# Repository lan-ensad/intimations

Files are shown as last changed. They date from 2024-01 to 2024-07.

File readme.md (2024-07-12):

# Intimations of Shanshui

<!-- TOC -->
- [Interactive Sculpture](#interactive-sculpture)
  - [Interaction & Space Mapping Logic](#interaction--space-mapping-logic)
  - [network diagram](#network-diagram)
  - [mechanics](#mechanics)
  - [electronics](#electronics)
- [Installation](#installation)
  - [Raspberry](#raspberry)
    - [DAC+](#dac)
    - [NodeRed](#nodered)
    - [Pure Data](#pure-data)
    - [Mosquitto](#mosquitto)
<!-- /TOC -->

## Interactive Sculpture



|||
|--|--|
|Artists/Creators|Vivian Wang, Martin De Bie, Olivier Bienz|
|Title, Year|Intimations of Shanshui, 2024|
|Exhibition Location|Shanshui: Echoes & Signals, M+ Hong Kong|
|Media|Interactive textile sculpture with sound, light, movement, and sensors|
|Logic/Description|For Intimations, we created a structural concept around the idea of circular layers. This sculpture crafted from fabric creates a focused and immersive experience blending sound, movement, and light. Variations in sound, light and movement respond to human presence and circumnavigation, unfolding in a slow and deliberate choreography of the different elements. The work is an ode to Shanshui painting, bridging tradition and modernity through an interactive exchange and the composition of textile and sound, with special detail given to how lighting dramatically alters the visual impact of the mountains.|
|||

### Interaction & Space Mapping Logic

There are 6 distance sensors on the sculpture. They are labelled S_00 to S_05. S_02 and S_05 are at the entry and exit points of the display location called the Breakout Room. To trigger sound and light activity, we partitioned the interaction zones into 6 zones labelled A, B, C, D, E and F.

**Sounds** are activated by presence within zones. All zones have an inner and an outer zone and these measurements are not the same for each zone. The rationale is to have something a little more organic in shape. For example, Zone D has an inner zone that goes up to 500mm, and its outer zone extends up to 2000mm whereas Zone F has an inner zone of 400mm and the outer extends only up to 1100mm. Anything outside of 1100mm will register a value on the sensor but it will not trigger a sound. We also programmed sounds to trigger when 2 zones register a value at the same time, meaning the sensors in these zones have to sense two separate persons in order to activate a sound. Certain sounds will also only trigger after a delay value of say 29656ms in the outer zone of Zone D. This gives some nuance and variation to the sounds and does not create cacophony for every interaction that happens each time a sensor value is registered. These 2-zone combinations are also varied between inner and outer zones. For each specific zone within zones A-F, there are also sometimes 2 or 3 files that are randomised to create more diverse combinations of sounds.

**Light** colour combinations are also varied. Each concentric circle has between 3-5 sectors of LEDs that light up. The colour sectors are irregular, so as to create organic combinations of light and shadow play between the layers of textile. Different behaviours are triggered depending of how many zones are active during a certain amount of time. Each colour sequence is scripted to create a sense of rhythm and movement and the colours are selected according to a predefined colour palette.

**Movement** of the 4 circular rings/layers of textile mountains are programmed and follow its own logic. Between 90000ms to 120000ms, different combinations of rings 1,2,3 will move. The duration of movement varies between 3000ms and 20000ms. The direction of the oscillation is randomised. The rings could move in the same direction or in opposite directions. Once a day, all 4 rings move.

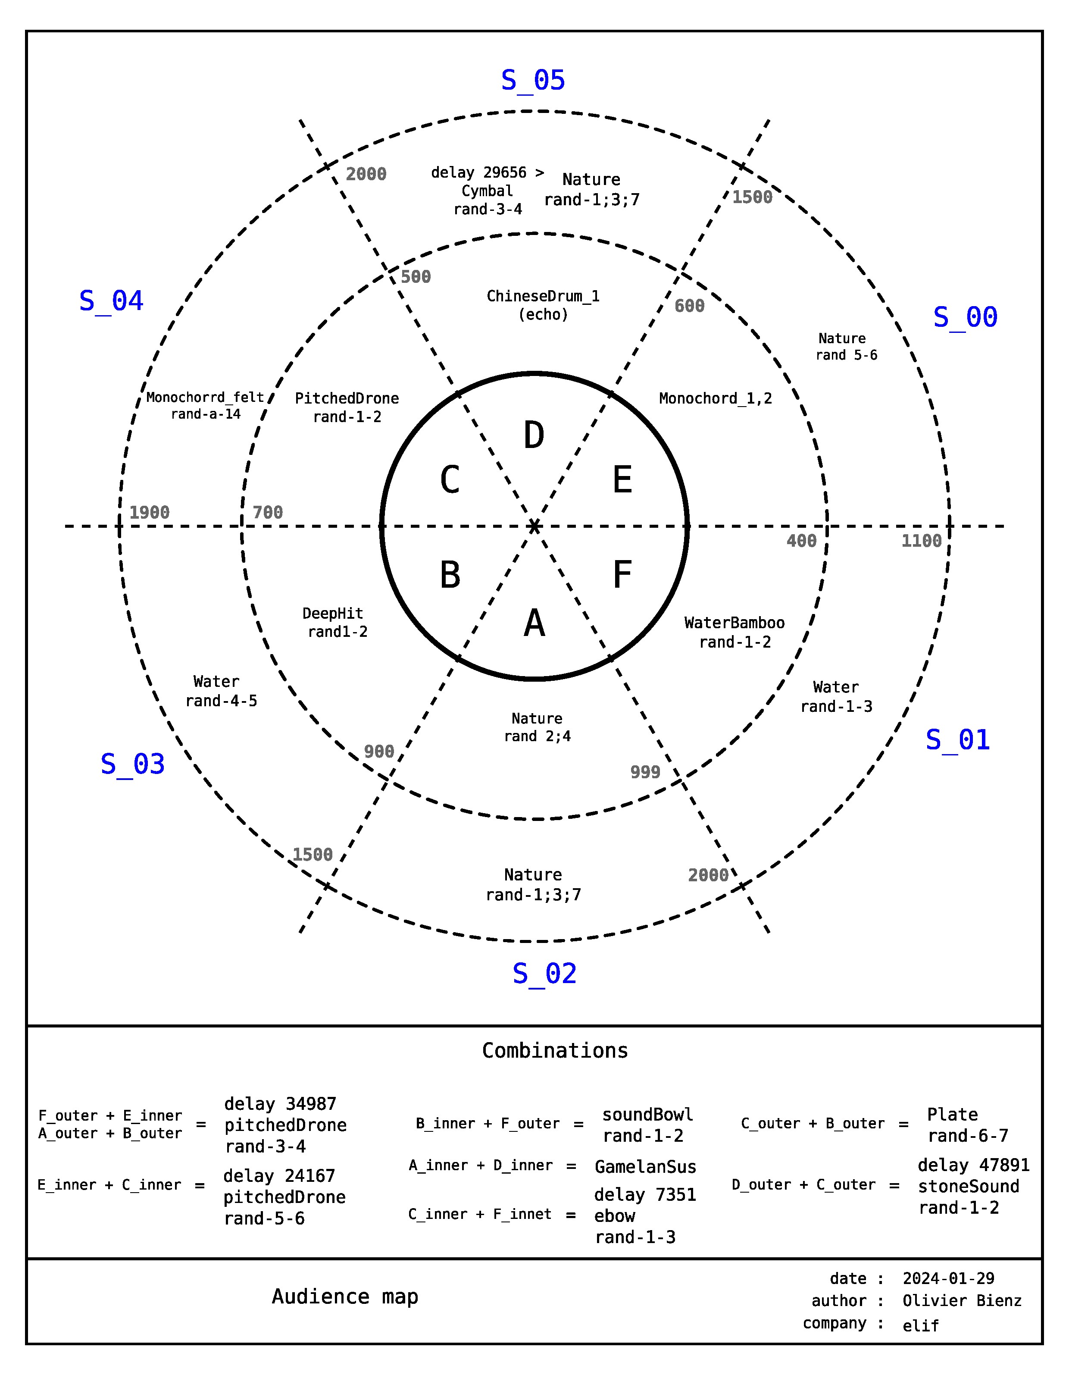
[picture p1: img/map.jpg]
map


### network diagram

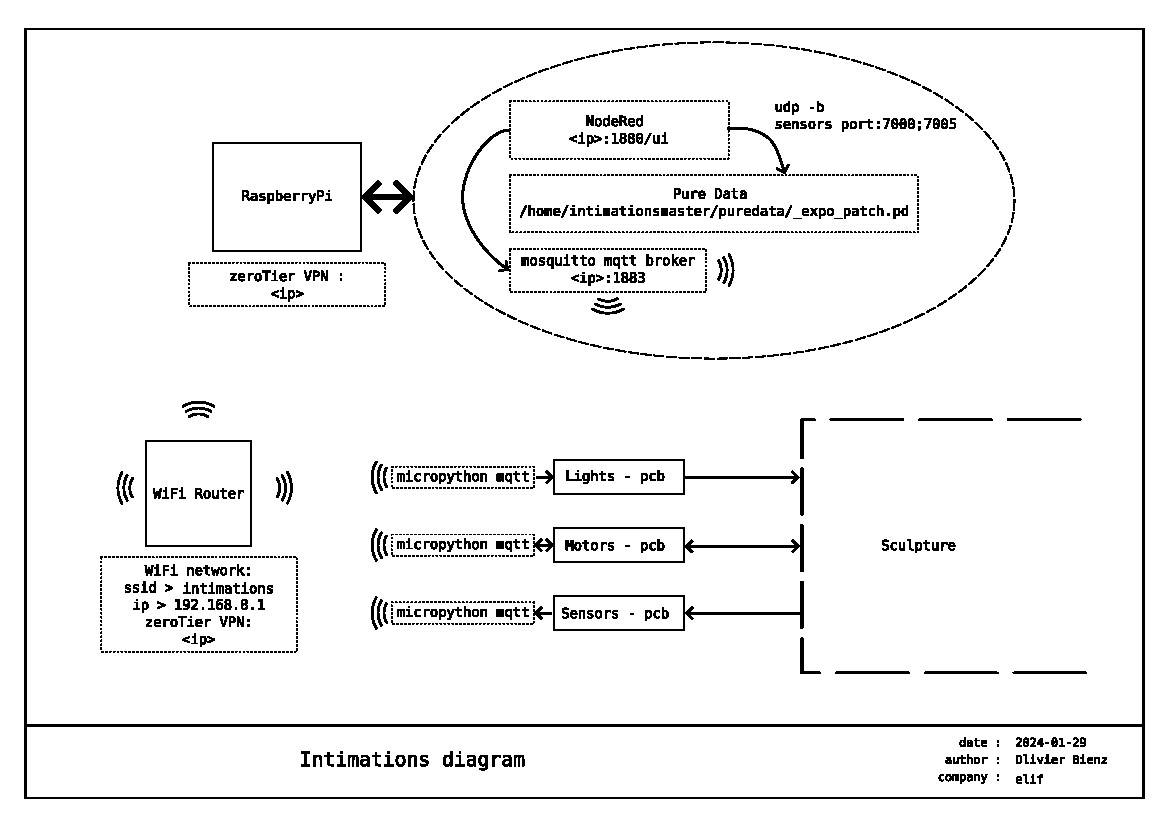
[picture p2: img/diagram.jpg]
diagram


### mechanics

Principles assembly

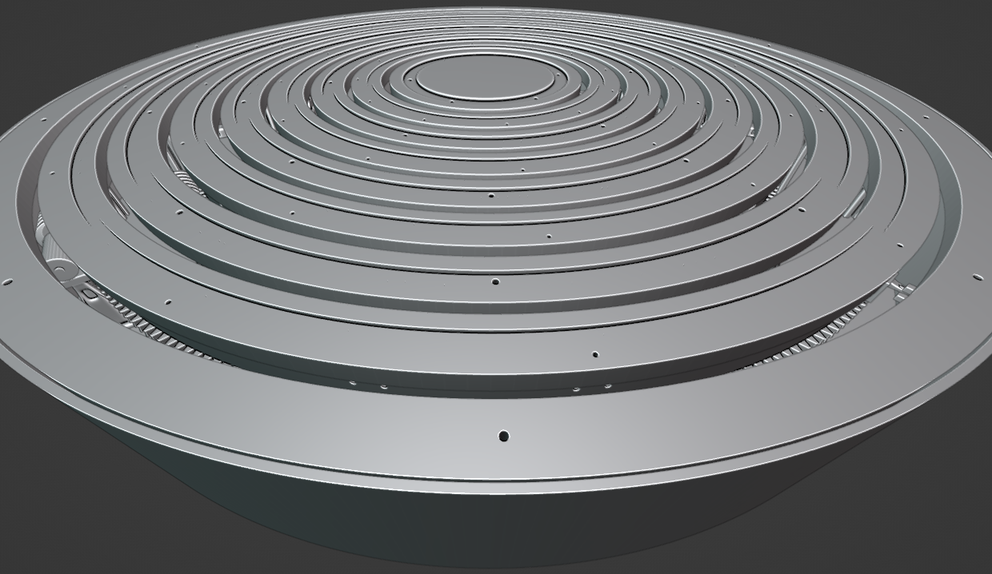
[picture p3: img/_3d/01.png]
full

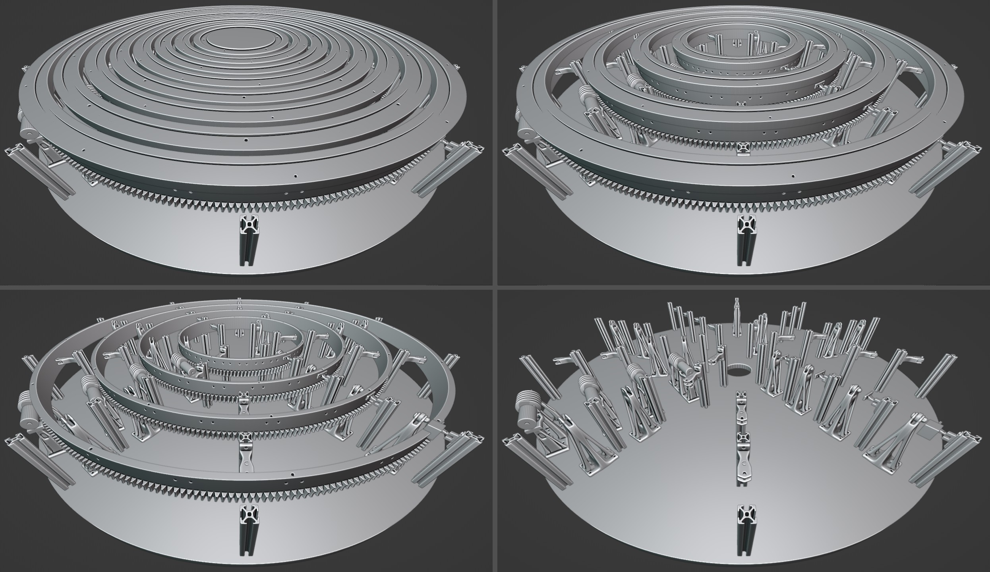
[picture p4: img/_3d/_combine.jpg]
combine


You can find all details and print parts in the *3d/* folder.

### electronics

**All firmeware available in *firmeware/< shield >* folder**\
**All schematics and gerber available in *pcb/mhk* folder in KiCad project format**

components :
- Global:
  - Raspberry Pi
  - [DAC+](https://www.raspberrypi.com/products/dac-plus/)
  - [router](https://www.gl-inet.com/products/gl-b1300/), setup for zeroTier vpn support
  - [PowerSupply +5V](https://www.meanwell.fr/ac-dc-ultra-slim-din-rail-power-supply-input-range-hdr--30--5), for the Raspberry Pi and the shields
  - [PowerSupply +12V](https://www.meanwell.fr/ac-dc-ultra-slim-din-rail-power-supply-input-range-hdr--30--12), for the router

- Motors Shield:
  - [dagu WT751](https://www.gotronic.fr/art-motoreducteur-wt751-17751.htm), motor 6Vcc
  - [drv8838](https://www.pololu.com/product/2990), driver motor, 0→11V
  - [optical endstop](https://www.amazon.fr/GeeekPi-Optical-Endstop-Photoelectric-imprimante/dp/B086P7XHJ2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)
  - [Raspberry Pico Wifi](https://www.raspberrypi.com/products/raspberry-pi-pico/), micropython

- Leds Shield:
  - WS2812 led strip, 5V
  - [Raspberry Pico Wifi](https://www.raspberrypi.com/products/raspberry-pi-pico/), micropython

- Sensors Shield:
  - [HC-SR04](https://www.gotronic.fr/art-module-de-detection-us-hc-sr04-20912.htm), ultrasonic sensors
  - [Raspberry Pico Wifi](https://www.raspberrypi.com/products/raspberry-pi-pico/), micropython

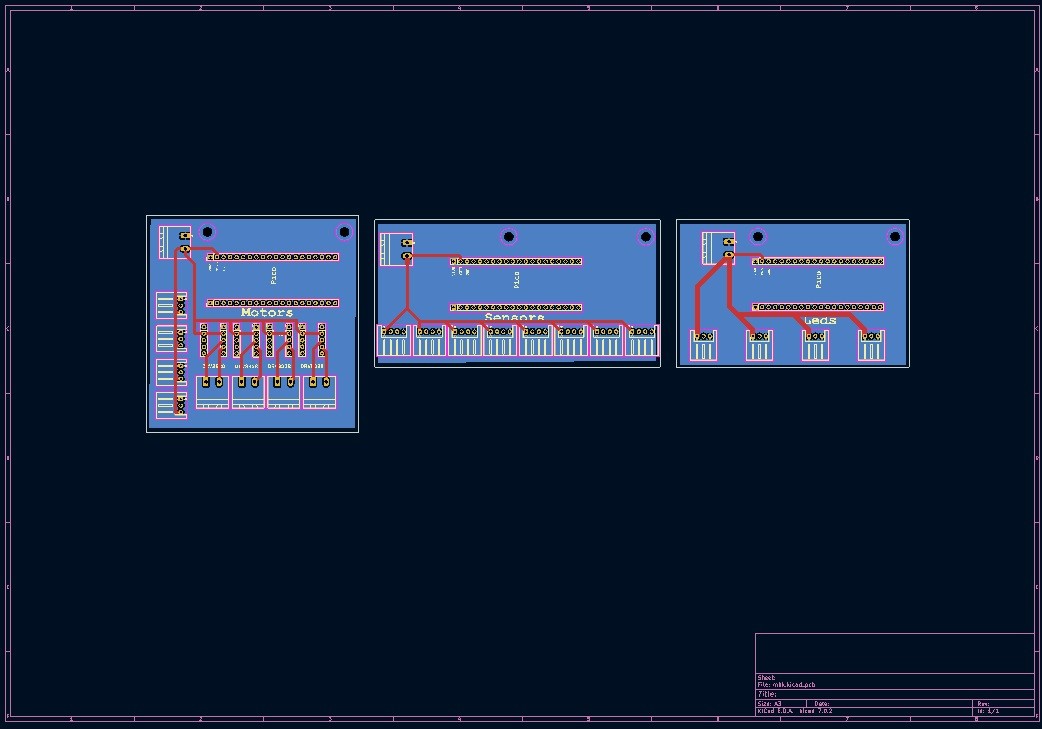
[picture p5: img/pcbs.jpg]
pcb

**All details available in *pcb/mhk* KiCad project**

## Installation

### Raspberry

#### DAC+

[dac+](https://www.raspberrypi.com/products/dac-plus/)

* Install \
  Plug the shield on the RaspberryPi

`sudo nano /boot/config.txt --line`

l.6. > comment `#dtparam=i2c_arm=on`\
l.7. > enable `dtparam=i2s=on`\
l.8. > comment `#dtparam=spi=on`\
l.11 > comment `#dtparam=audio=on`\
l.12 > enable `dtoverlay=iqaudio-dac`\
l.27 > verify `dtoverlay=vc4-kms-v3d,noaudi` > (cut hdmi audio)

**All config files are in *dacplus/config.txt* folder**

#### NodeRed

* Install \
  [NodeRed](https://nodered.org/docs/getting-started/raspberrypi)
* Install dashboard \
  Palette > Install > *node-red-dashboard*

**The flow is available in the *nodered/flows.json* folder.**

#### Pure Data

* Install

```
sudo apt update && sudo apt upgrade -y

sudo apt install puredata -y
```

**The patch is available in the *puredata/_expo_patch.pd* folder.**

#### Mosquitto

* Install

```
sudo apt update && sudo apt upgrade -y

sudo apt install mosquitto mosquitto-clients -y

sudo systemctl enable mosquitto.service
```

* Edit config \
  `sudo nano /etc/mosquitto/mosquitto.conf`

add in the end :

```
listener 1883
allow_anonymous true
```

**Check the installation :**
* subscribe command line \
  `mosquitto_sub -d -t <topic>` (anonymous)\
  `mosquitto_sub -d -t <topic> -u <user> -P <pass>` (logged)
* publish command line \
  `mosquitto_pub -d -t <topic> -m "<Message>"` (anonymous)\
  `mosquitto_pub -d -t <topic> -m "<Message>" -u <user> -P <pass>` (logged)

  #### WIFI

`sudo nano /etc/wpa_spplicant/wpa_supplicant.conf`

```
network{
  scan_ssid=1
  ssid="<SSID>"
  psk="<PASSWORD>"
  key_mgmt=WPA-PSK
}
```

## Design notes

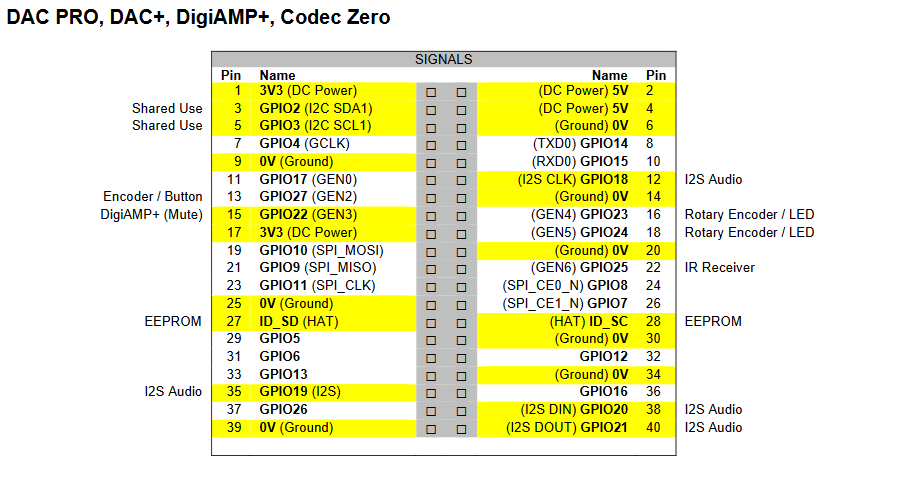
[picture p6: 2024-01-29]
pcb/pinmap_dac+.png

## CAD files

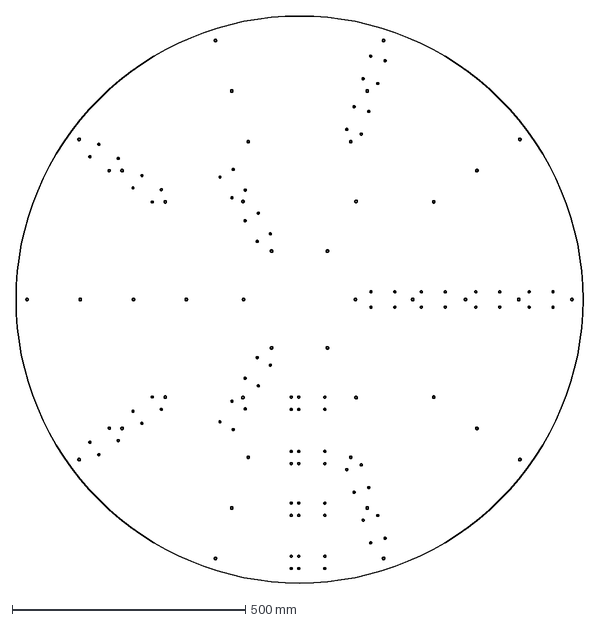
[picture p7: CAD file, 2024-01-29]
3d/milling_parts/bottom.dxf
1215.0 x 1215.0 mm

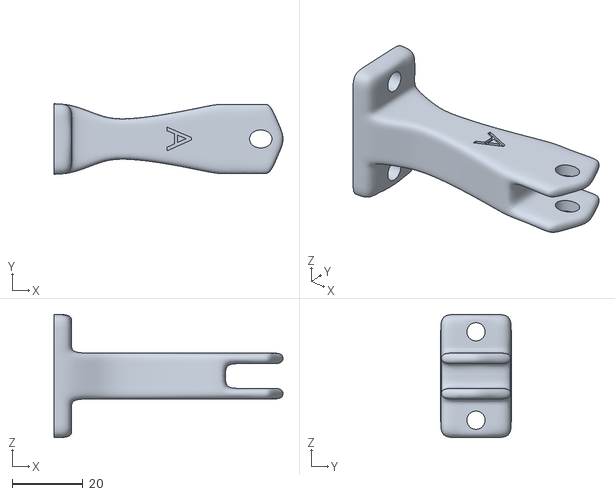
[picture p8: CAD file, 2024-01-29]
3d/print_parts/bearing_support/lock_side_A.stl
65.0 x 20.0 x 35.0

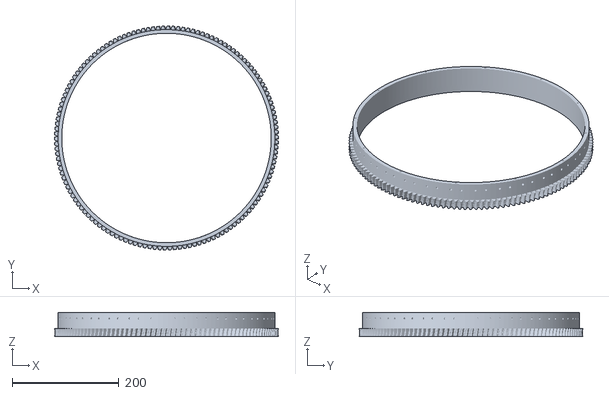
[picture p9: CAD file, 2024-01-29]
3d/print_parts/gears/gear_A.stl
420.0 x 420.0 x 45.7

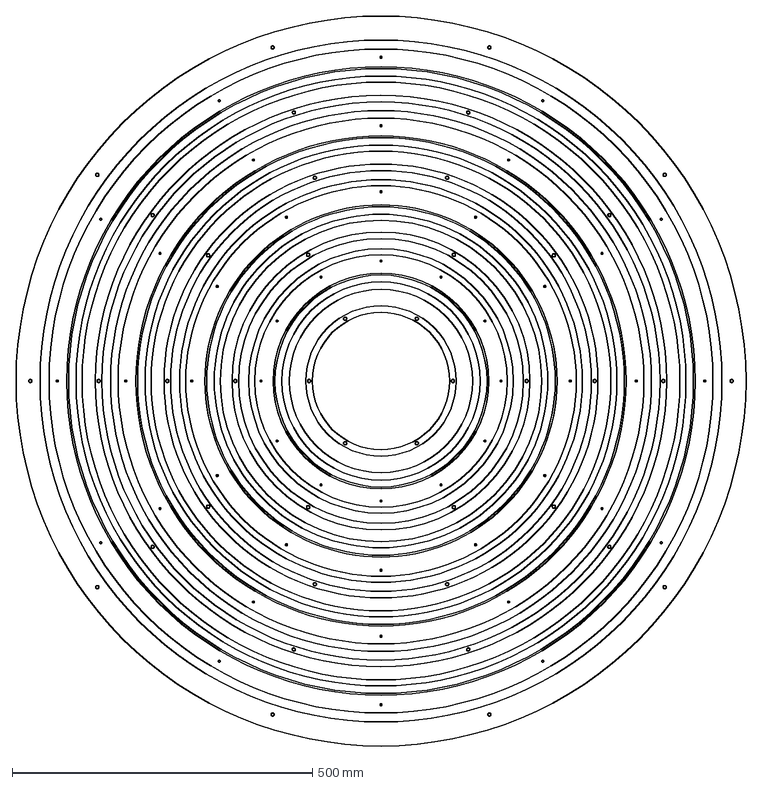
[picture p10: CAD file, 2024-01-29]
3d/milling_parts/top.dxf
1215.0 x 1215.0 mm

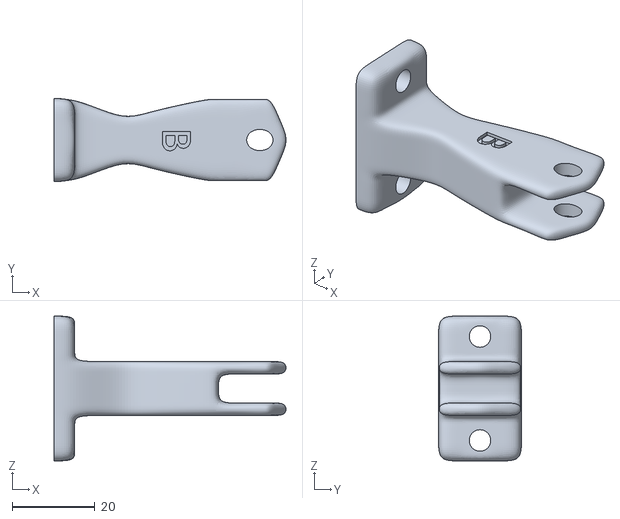
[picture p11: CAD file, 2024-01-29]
3d/print_parts/bearing_support/lock_side_B.stl
56.0 x 20.0 x 35.0

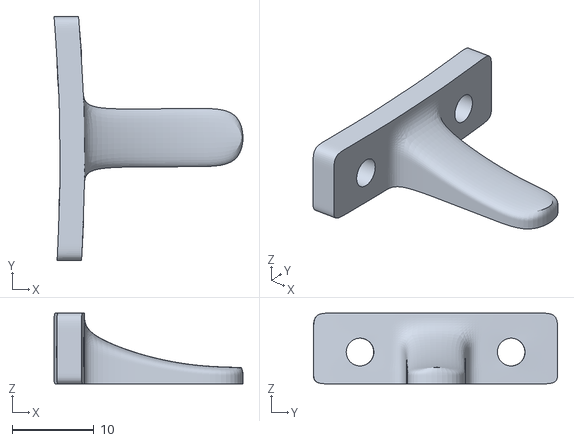
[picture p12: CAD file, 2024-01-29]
3d/print_parts/endstops/endstop_trigger.stl
23.1 x 29.9 x 8.67

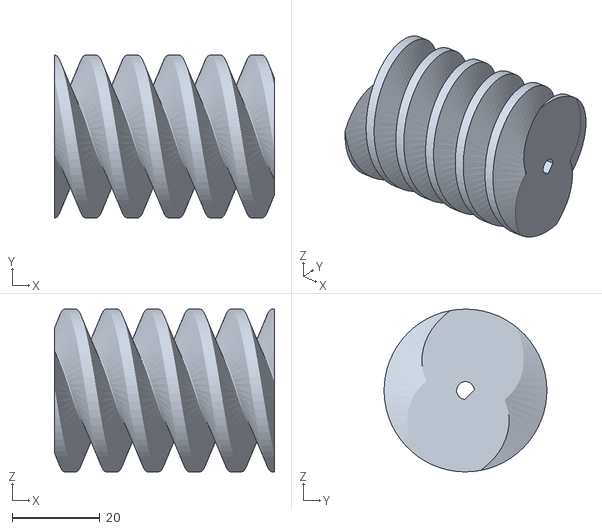
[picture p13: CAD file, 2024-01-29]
3d/print_parts/gears/worm_gear.stl
50.0 x 37.0 x 37.0

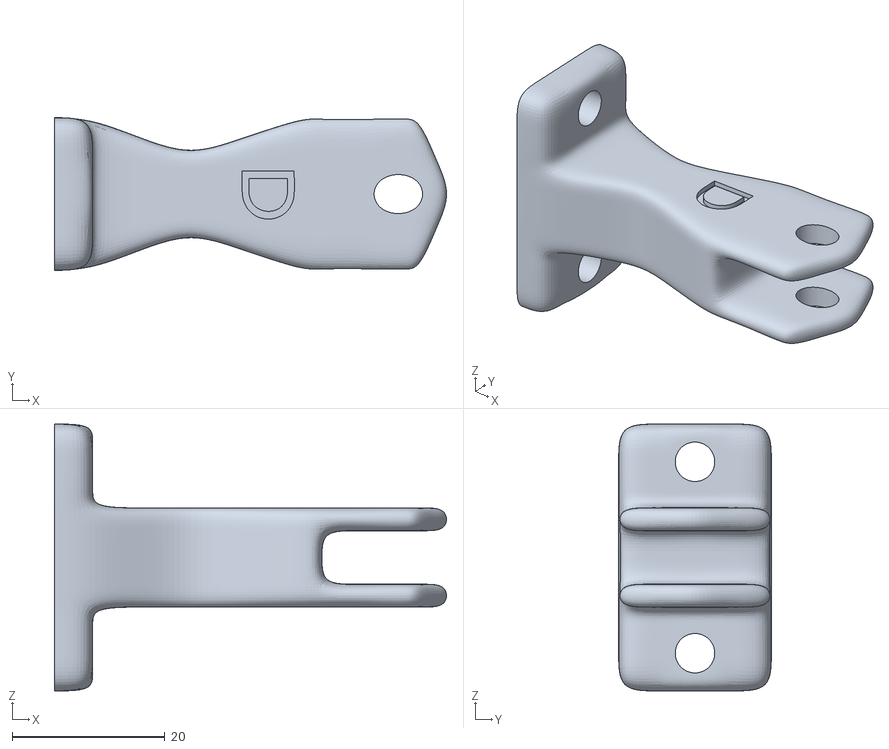
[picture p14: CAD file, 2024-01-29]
3d/print_parts/bearing_support/lock_side_D.stl
51.4 x 20.0 x 35.0

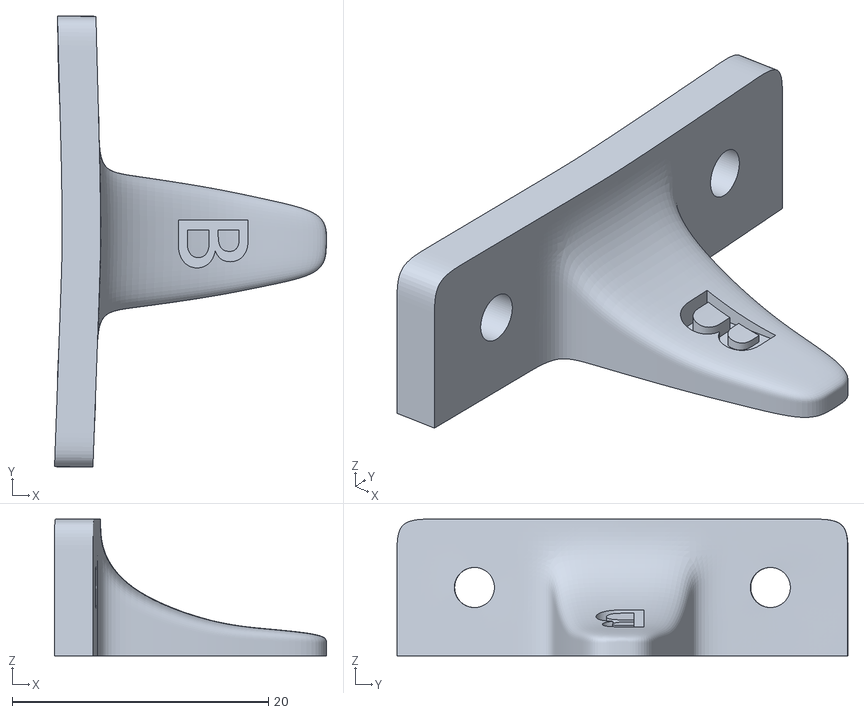
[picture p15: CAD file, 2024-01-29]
3d/print_parts/endstops/endstop_trigger_B.stl
21.2 x 35.2 x 10.7

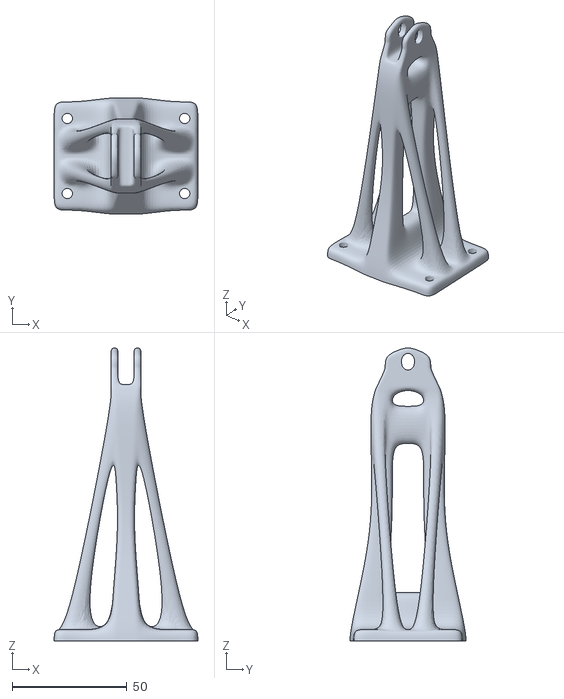
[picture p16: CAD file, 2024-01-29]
3d/print_parts/bearing_support/lock_top.stl
62.7 x 50.8 x 127.8

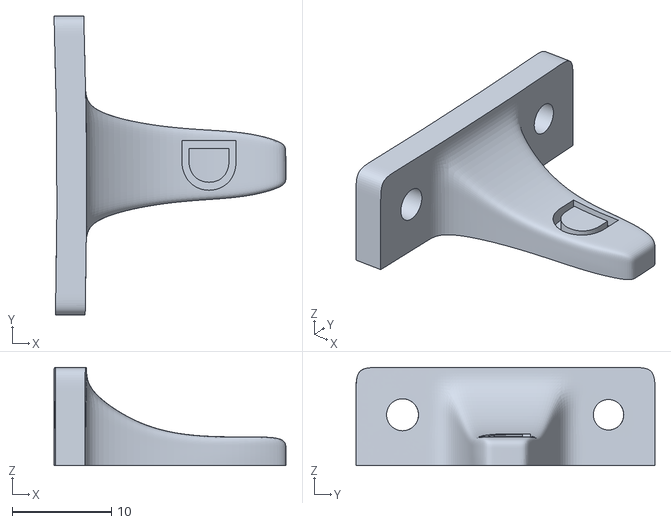
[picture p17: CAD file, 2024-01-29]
3d/print_parts/endstops/endstop_trigger_D.stl
23.4 x 30.1 x 9.89

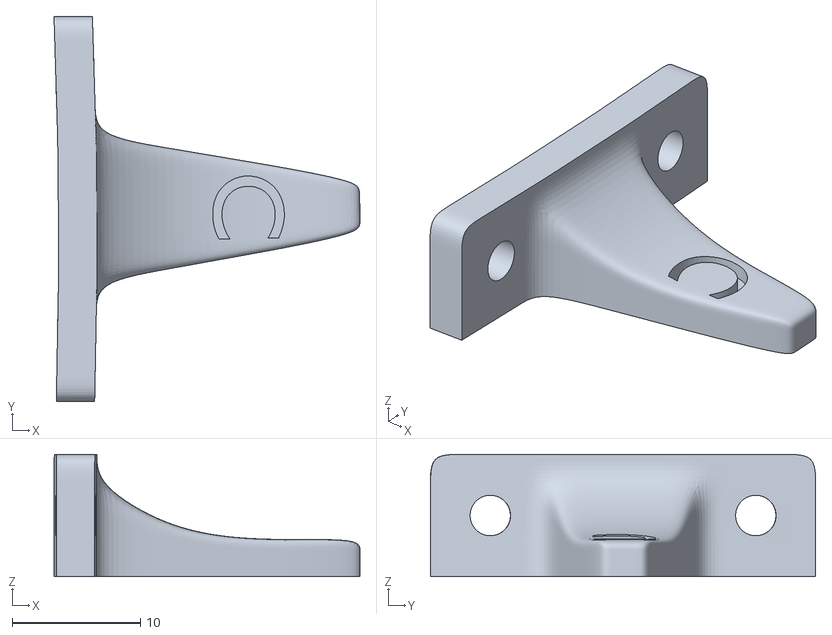
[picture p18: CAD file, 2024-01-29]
3d/print_parts/endstops/endstop_trigger_C.stl
23.9 x 30.1 x 9.54

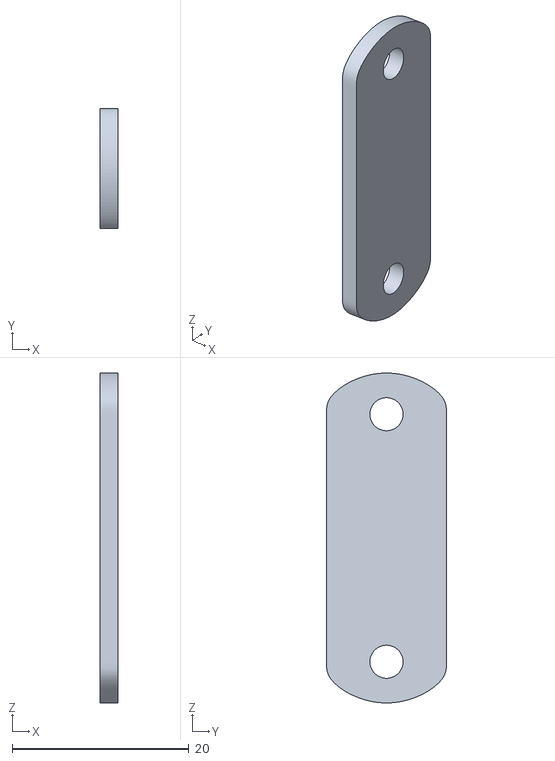
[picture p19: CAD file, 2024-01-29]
3d/print_parts/endstops/endstop_supp.stl
2.00 x 13.6 x 37.3

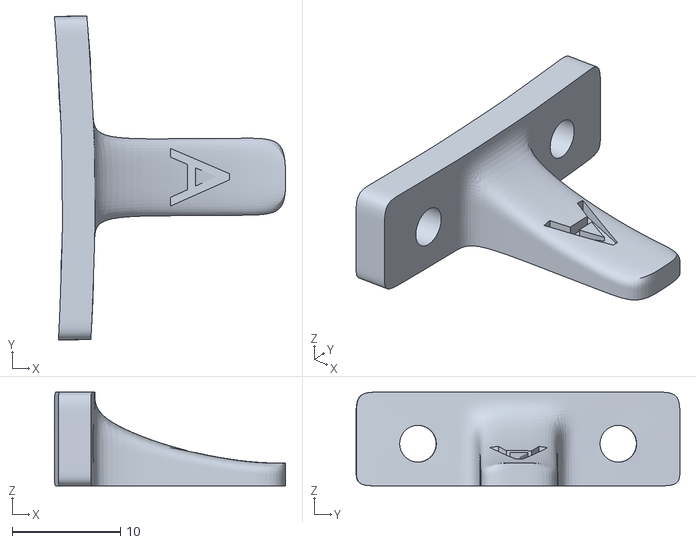
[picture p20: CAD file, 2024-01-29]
3d/print_parts/endstops/endstop_trigger_A.stl
21.4 x 29.9 x 8.67

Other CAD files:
3d/print_parts/bearing_support/lock_side_C.stl
3d/print_parts/endstops/endstop_nut_.stl

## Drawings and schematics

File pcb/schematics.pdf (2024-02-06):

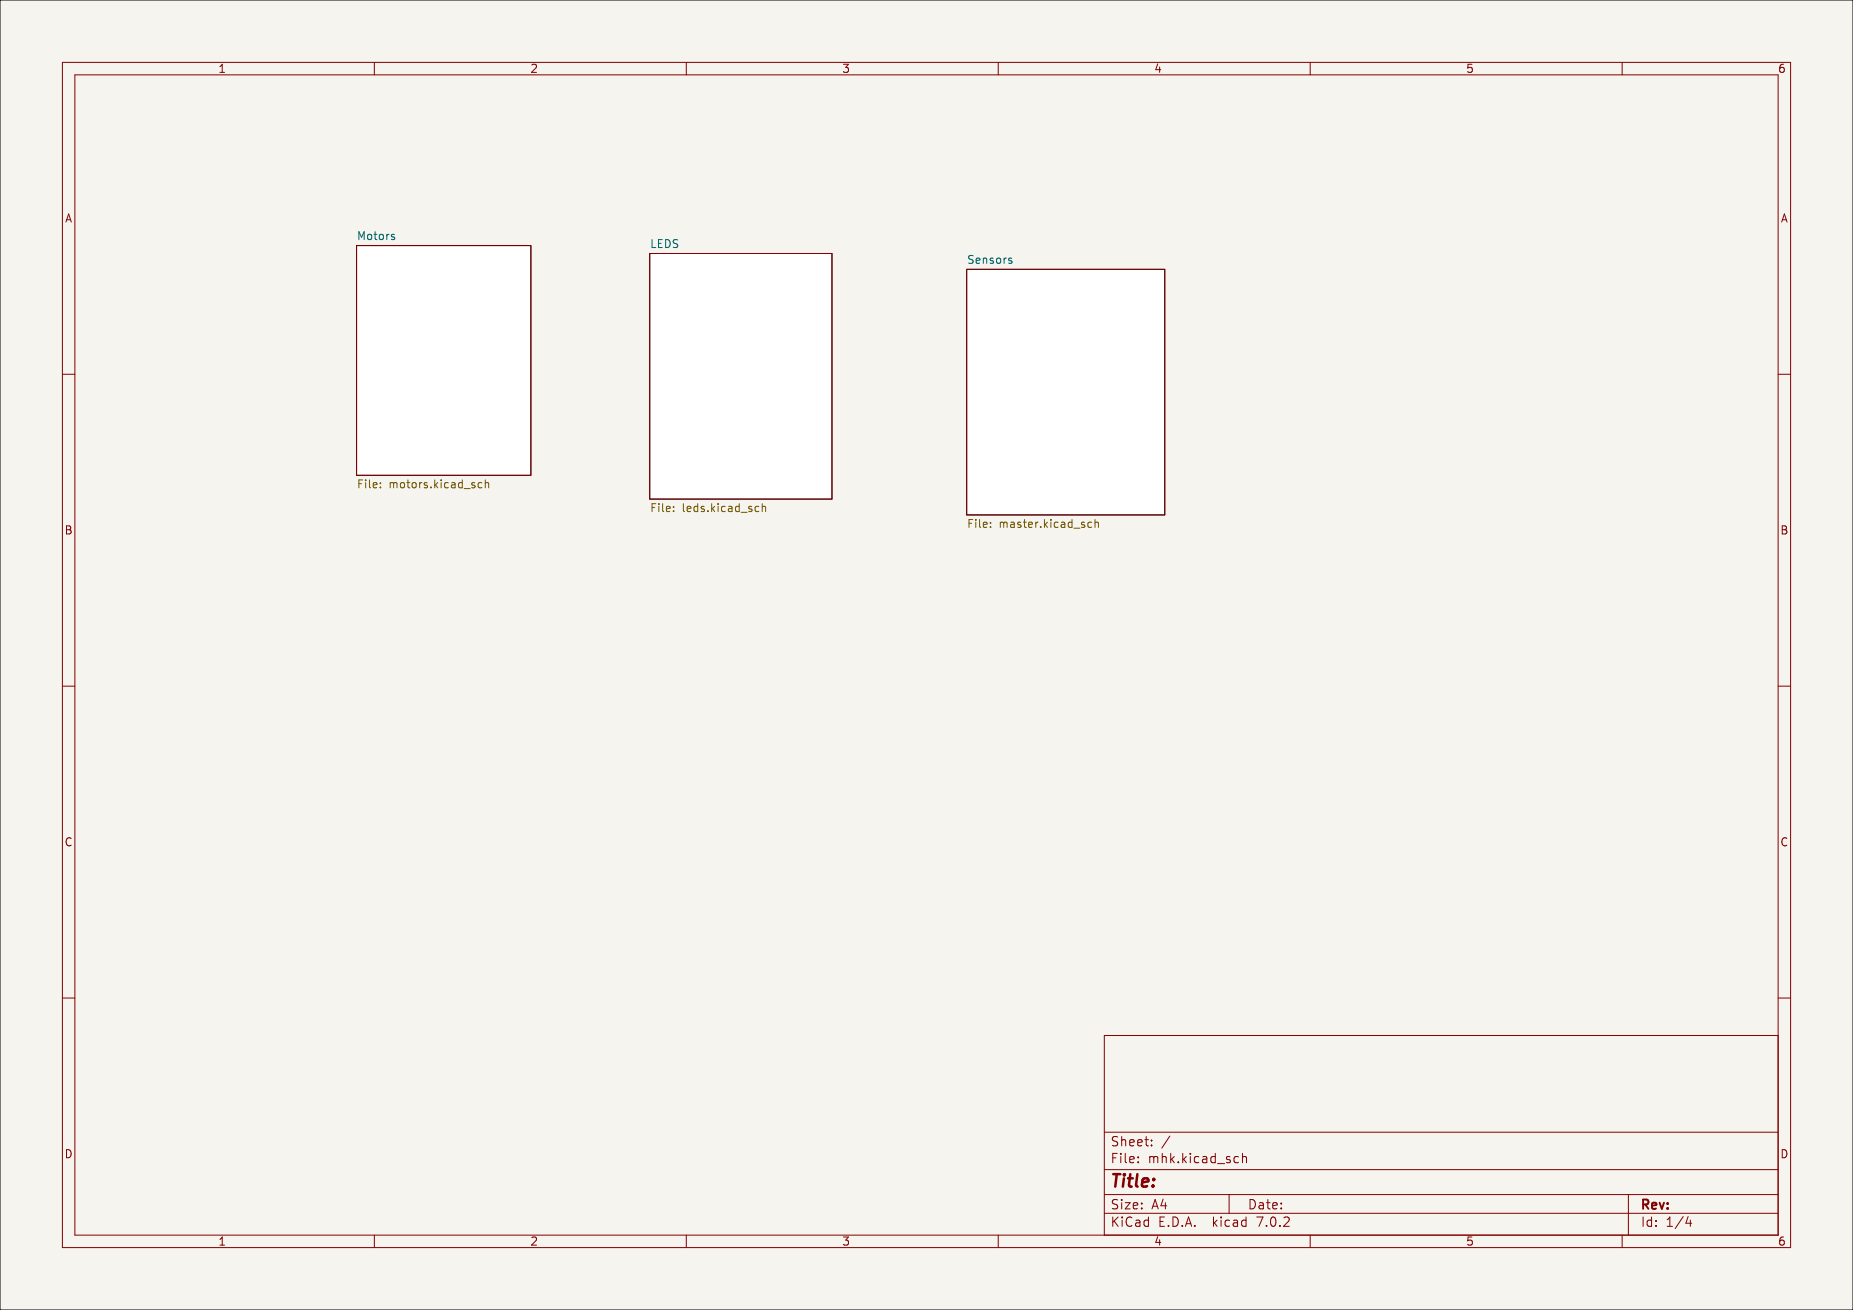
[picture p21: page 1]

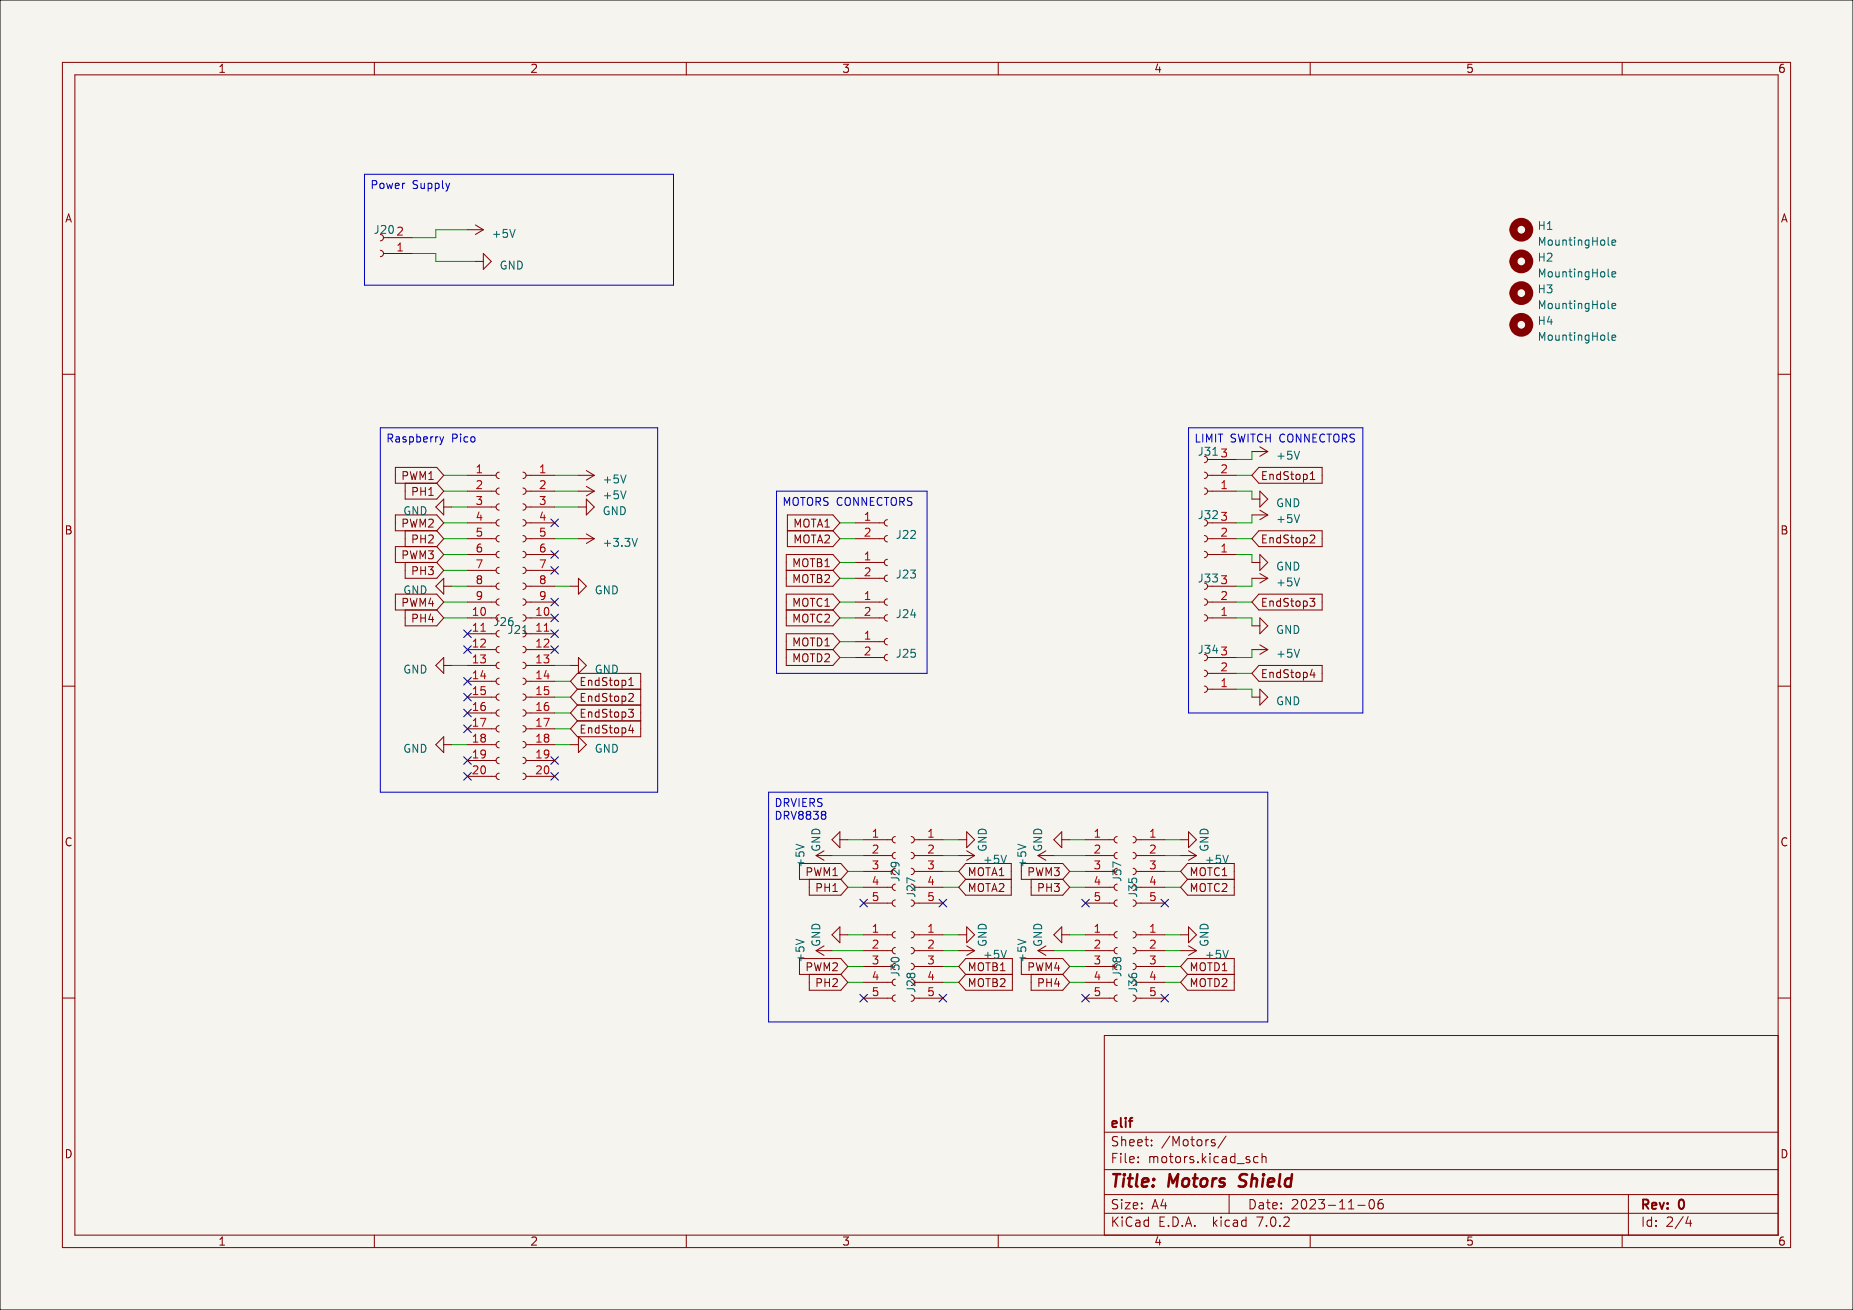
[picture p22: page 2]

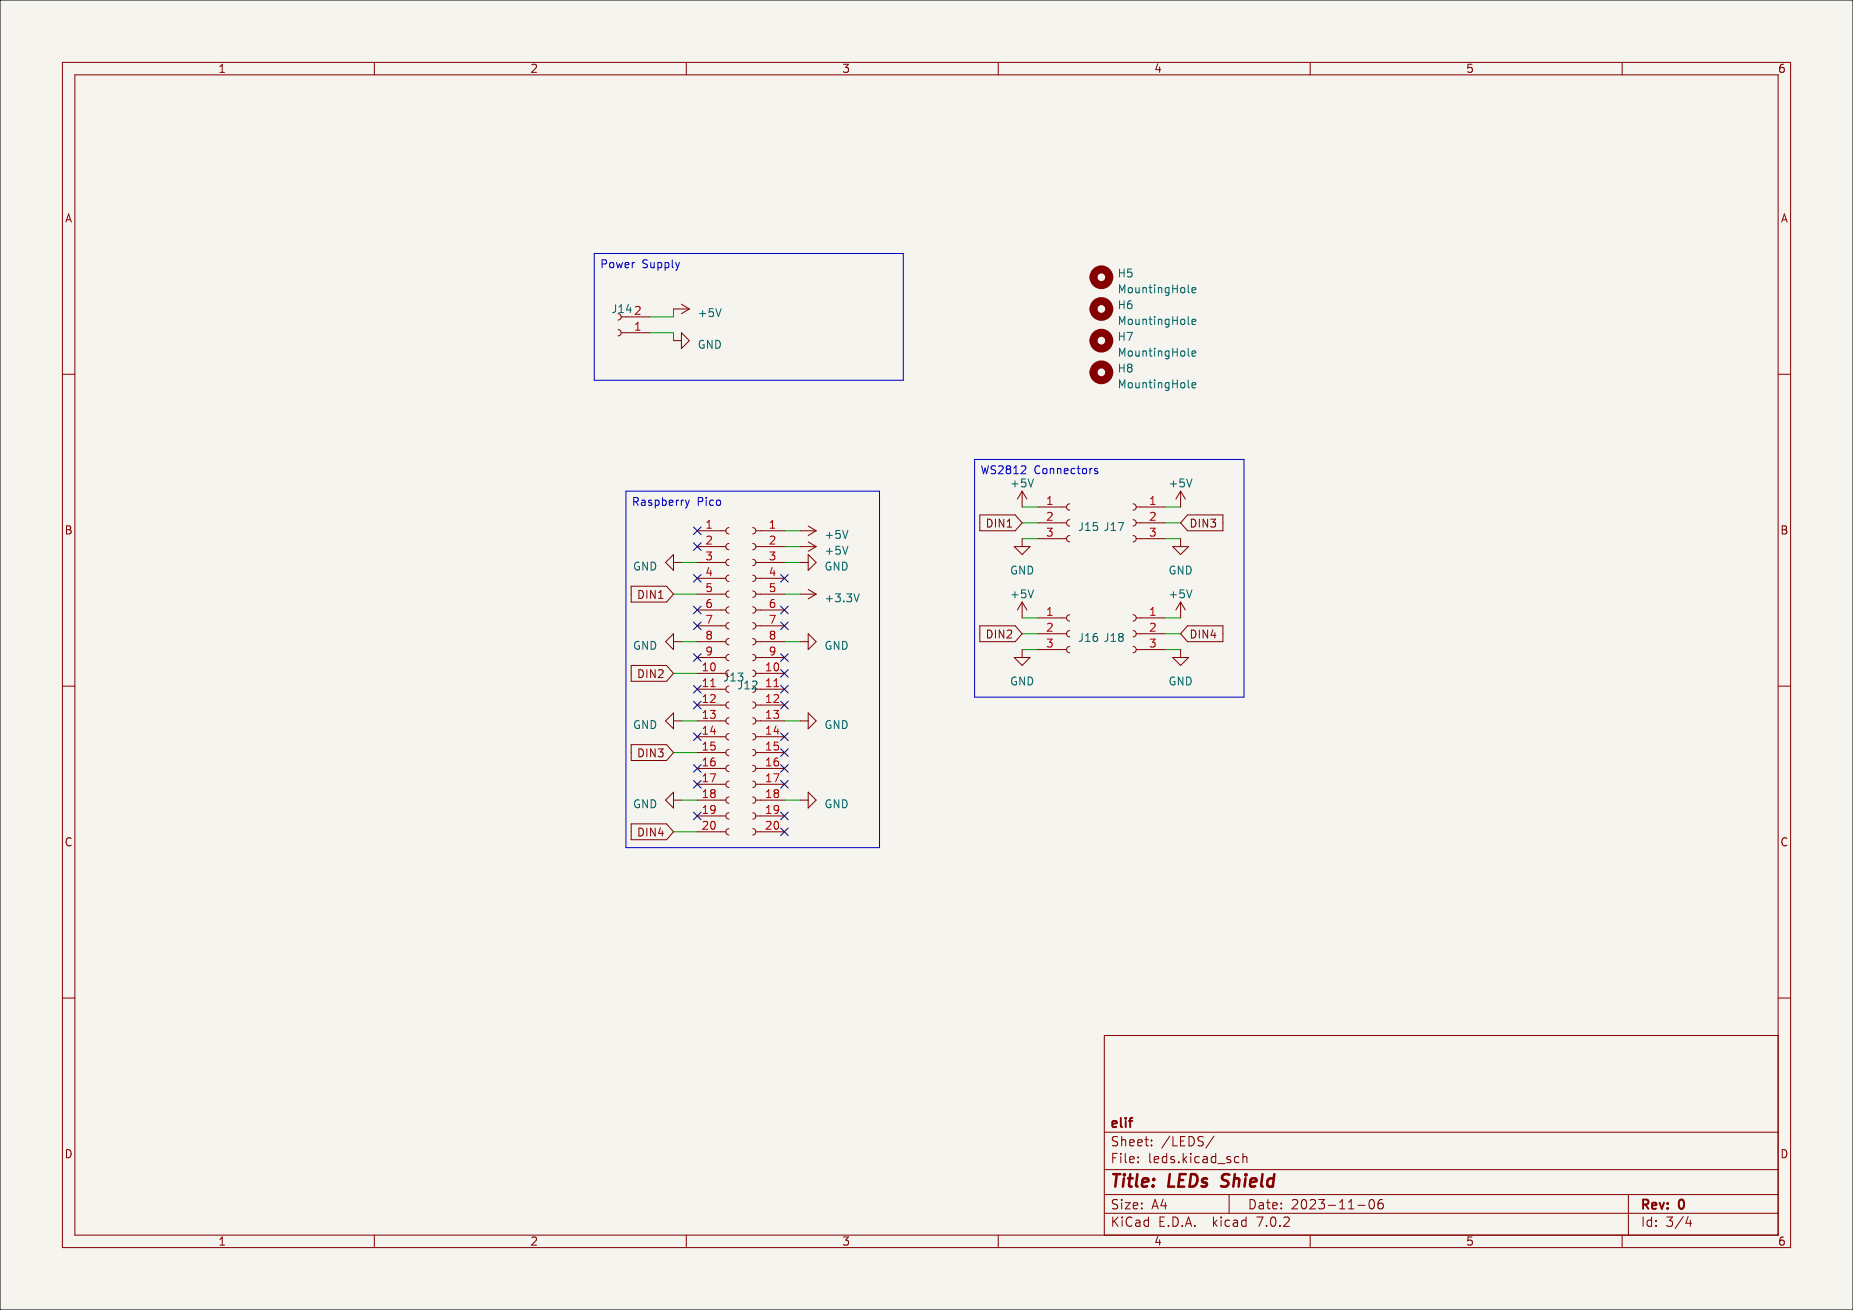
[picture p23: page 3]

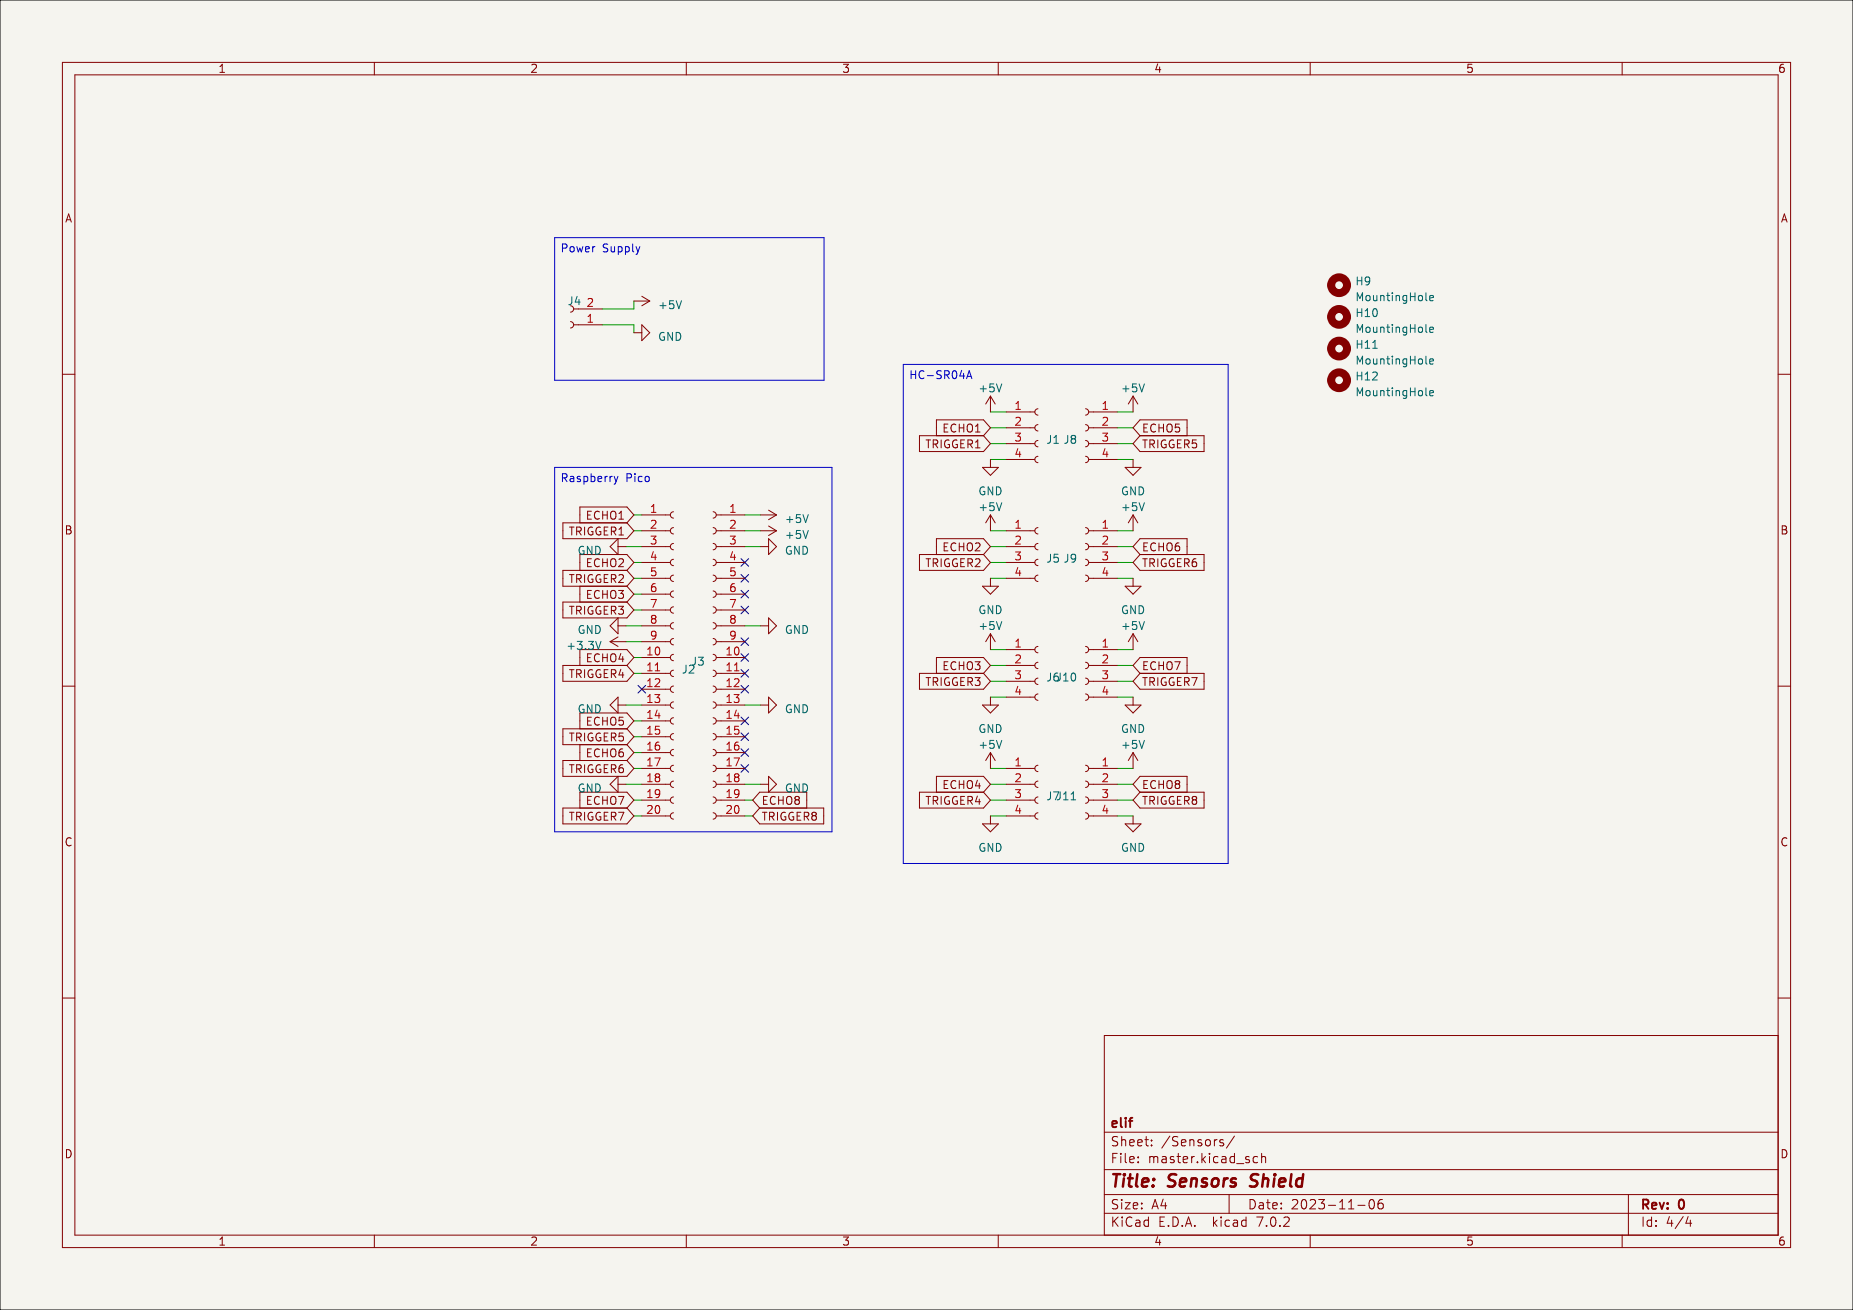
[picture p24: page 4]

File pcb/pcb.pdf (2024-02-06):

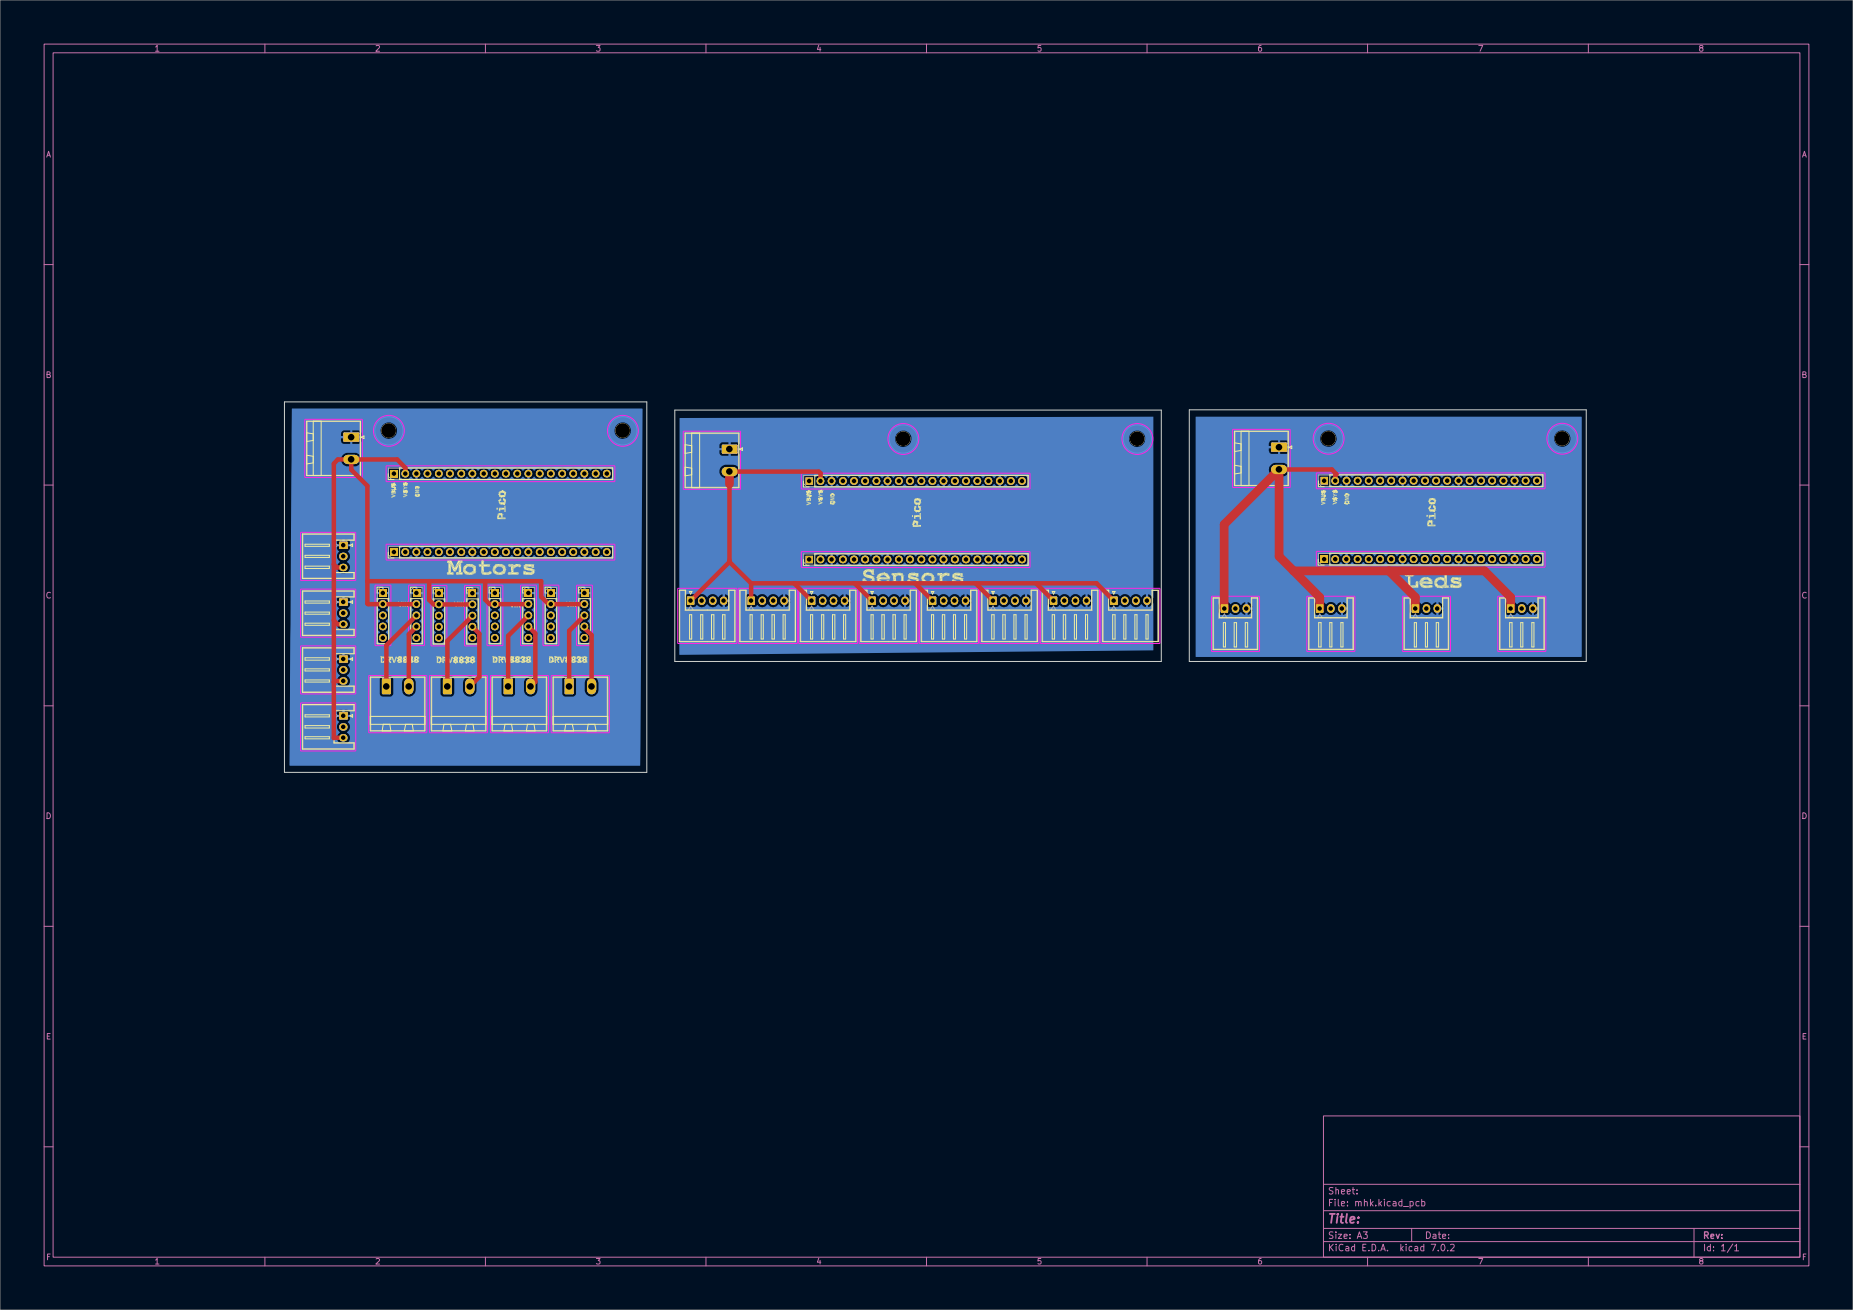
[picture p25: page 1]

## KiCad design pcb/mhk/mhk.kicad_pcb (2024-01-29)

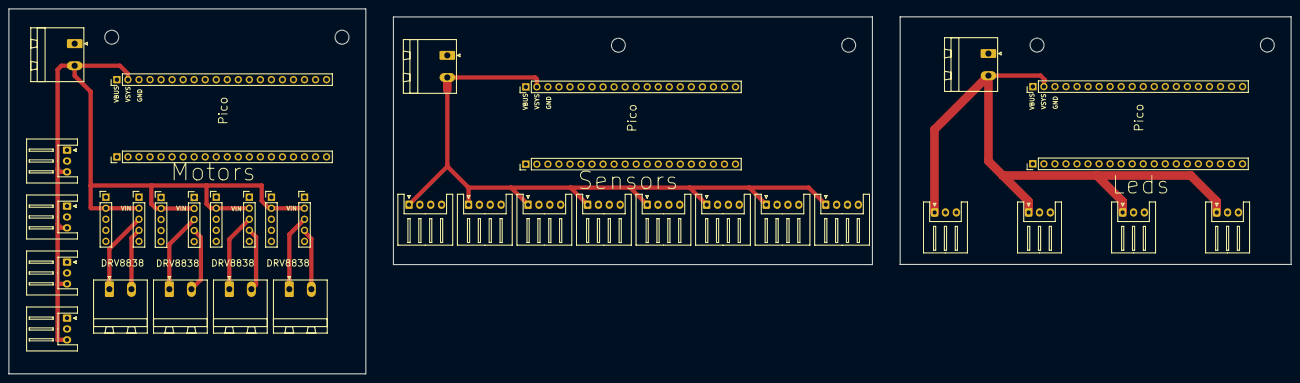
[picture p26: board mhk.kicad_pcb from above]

Board: 4 copper layers, 295.1 x 84.0 mm, 43 parts (0 on the bottom side), 43 nets.

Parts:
H1, H1#2, H1#3, H2, H2#2, H2#3: MountingHole; MountingHole_3.2mm_M3
J1, J5, J6, J7, J8, J9, J10, J11: Conn_01x04_Socket; JST_XH_S4B-XH-A_1x04_P2.50mm_Horizontal
J2, J3, J12, J13, J21, J26: Conn_01x20_Socket; PinHeader_1x20_P2.54mm_Vertical
J4, J14, J20, J22, J23, J24, J25: Conn_01x02_Socket; PhoenixContact_MSTBA_2,5_2-G-5,08_1x02_P5.08mm_Horizontal
J15, J16, J17, J18, J31, J32, J33, J34: Conn_01x03_Socket; JST_XH_S3B-XH-A_1x03_P2.50mm_Horizontal
J27, J28, J29, J30, J35, J36, J37, J38: Conn_01x05_Socket; PinHeader_1x05_P2.54mm_Vertical

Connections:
+3.3V: J2.9, J13.5, J26.5
+5V: J1.1, J3.1, J3.2, J4.2, J5.1, J6.1, J7.1, J8.1, J9.1, J10.1, J11.1, J13.1, J13.2, J14.2, J15.1, J16.1, J17.1, J18.1, J20.2, J26.1, J26.2, J27.2, J28.2, J29.2, J30.2, J31.3, J32.3, J33.3, J34.3, J35.2, J36.2, J37.2, J38.2
DIN1: J12.5, J15.2
DIN2: J12.10, J16.2
DIN3: J12.15, J17.2
DIN4: J12.20, J18.2
ECHO1: J1.2, J2.1
ECHO2: J2.4, J5.2
ECHO3: J2.6, J6.2
ECHO4: J2.10, J7.2
ECHO5: J2.14, J8.2
ECHO6: J2.16, J9.2
ECHO7: J2.19, J10.2
ECHO8: J3.19, J11.2
EndStop1: J26.14, J31.2
EndStop2: J26.15, J32.2
EndStop3: J26.16, J33.2
EndStop4: J26.17, J34.2
GND: J1.4, J2.3, J2.8, J2.13, J2.18, J3.3, J3.8, J3.13, J3.18, J4.1, J5.4, J6.4, J7.4, J8.4, J9.4, J10.4, J11.4, J12.3, J12.8, J12.13, J12.18, J13.3, J13.8, J13.13, J13.18, J14.1, J15.3, J16.3, J17.3, J18.3, J20.1, J21.3, J21.8, J21.13, J21.18, J26.3, J26.8, J26.13, J26.18, J27.1, J28.1, J29.1, J30.1, J31.1, J32.1, J33.1, J34.1, J35.1, J36.1, J37.1, J38.1
MOTA1: J22.1, J29.3
MOTA2: J22.2, J29.4
MOTB1: J23.1, J30.3
MOTB2: J23.2, J30.4
MOTC1: J24.1, J37.3
MOTC2: J24.2, J37.4
MOTD1: J25.1, J38.3
MOTD2: J25.2, J38.4
PH1: J21.2, J27.4
PH2: J21.5, J28.4
PH3: J21.7, J35.4
PH4: J21.10, J36.4
PWM1: J21.1, J27.3
PWM2: J21.4, J28.3
PWM3: J21.6, J35.3
PWM4: J21.9, J36.3
TRIGGER1: J1.3, J2.2
TRIGGER2: J2.5, J5.3
TRIGGER3: J2.7, J6.3
TRIGGER4: J2.11, J7.3
TRIGGER5: J2.15, J8.3
TRIGGER6: J2.17, J9.3
TRIGGER7: J2.20, J10.3
TRIGGER8: J3.20, J11.3

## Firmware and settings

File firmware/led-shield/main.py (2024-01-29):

from neopixel import Neopixel
from umqttsimple import MQTTClient
import ubinascii
import machine
import time
import json

# ### BLINK STATE ###
led = machine.Pin("LED", machine.Pin.OUT)
timer = machine.Timer()
def blink(timer):
    led.toggle()
timer.init(period=1000, mode=machine.Timer.PERIODIC, callback=blink)

# ### MQTT ###
SERVER = '<MQTT SERVER IP>'
CLIENT_ID = ubinascii.hexlify(machine.unique_id())
mqttClient = MQTTClient(CLIENT_ID, SERVER)
mqttClient.connect()

# ### COLORS ###
cold_white=(225, 225, 225)
warm_white=(245, 175, 100)
red = (255, 10, 0)
orange = (200, 50, 0)
yellow = (200, 175, 0)
green = (5, 225, 5)
blue = (10, 10, 225)
violet = (100, 0, 90)
rgbAll = [cold_white, warm_white, red, orange, yellow, green, blue, violet]

brightnessFader=[0, 0, 0, 0]
faderAmount=[0, 0, 0, 0]
strips = [
    Neopixel(num_leds=45, state_machine=3, pin=3, mode='GRB'),
    Neopixel(num_leds=91, state_machine=7, pin=7, mode='GRB'),
    Neopixel(num_leds=134, state_machine=0, pin=11, mode='GRB'),
    Neopixel(num_leds=178, state_machine=1, pin=15, mode='GRB')
]
##      LED SECTORS
##  A,B,C,D : 0→full ring ++
## A→3    B→3   C→5     D→5
ledsectors=[
    [
        [0, 45],
        [0, 15],
        [12,35],
        [28, 45]
    ],
    [
        [0, 91],
        [0, 35],
        [18, 55],
        [50, 91]
    ],
    [
        [0,134],
        [0,65],
        [35,91],
        [53,101],
        [23,71],
        [92,134]
    ],
    [
        [0,178],
        [0,42],
        [23,59],
        [47,91],
        [81,117],
        [111,178],
    ]
]
# ### STRIP FUNCTIONS ###
def allColor(strip, t, bright):
    count = 0
    while True:
        if count>=len(rgbAll):
            count = 0
        strips[strip].clear()
        strips[strip].fill(rgbAll[count], bright)
        strips[strip].show()
        print(rgbAll[count])
        time.sleep(t)
        count +=1
def fillOne(strip, col, bright):
    strips[strip].clear()
    strips[strip].brightness(bright)
    strips[strip].fill(rgbAll[col])
    strips[strip].show()
def resetAll():
    for i in range(4):
        strips[i].clear()
        strips[i].show()
def resetOne(strip):
    global brightnessFader
    brightnessFader[strip]=0
    for i in range(strips[strip].num_leds):
        strips[strip].clear()
        strips[strip].show()
def segOneFix(strip, start, end, col, bright):
    resetOne(strip)
    strips[strip].brightness(bright)
    for i in range(start, end):
        strips[strip].set_pixel(i, rgbAll[col])
        strips[strip].show()
def snaking(strip, t):
    while True:
        for i in range(strips[strip].num_leds):
            strips[strip].clear()
            strips[strip].set_pixel(i, orange, 50)
            strips[strip].show()
            time.sleep(t)
def segOneFade(strip, start, end, tick, amount, col):
    global brightnessFader
    global faderAmount
    brightnessFader[strip]=0
    faderAmount[strip]=amount
    while True:
        brightnessFader[strip]+=faderAmount[strip]
        if brightnessFader[strip]>=200 or brightnessFader[strip]<=0:
            faderAmount[strip]*=-1
        strips[strip].brightness(brightnessFader[strip])
        for i in range(start, end):
            strips[strip].set_pixel(i, rgbAll[col])
            strips[strip].show()
            time.sleep_ms(tick)


# ### MAIN CALLBACK ###
def sub_cb(topic, msg):
    # ###  PARSE JSON  ###
    data = ""
    for i in msg:
        data += chr(i)
    data_j = json.loads(data)
    index = int(data_j.get('index')['payload'])
    colour = int(data_j.get('color')['payload'])
    sector = int(data_j.get('sector')['payload'])
    brightness= int(data_j.get('brightness')['payload'])
    if brightness <= 1:
        resetOne(index)
        print(f'reset strip n°{index}')
    else:
        segOneFix(index, ledsectors[index][sector][0], ledsectors[index][sector][1], colour, brightness)
        print(f'strip : {index} on sector : {sector} : {rgbAll[colour]} at {brightness}')

TOPIC = "leds"
mqttClient.set_callback(sub_cb)
mqttClient.subscribe(TOPIC)
print("Connected to %s, subscribed to %s topic" % (SERVER, TOPIC))

def main():
    while True:
        mqttClient.check_msg()

if __name__ == "__main__":
    main()

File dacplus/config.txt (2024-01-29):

# For more options and information see
 2 # http://rptl.io/configtxt
 3 # Some settings may impact device functionality. See link above for details
 4
 5 # Uncomment some or all of these to enable the optional hardware interfaces
 6 #dtparam=i2c_arm=on
 7 dtparam=i2s=on
 8 #dtparam=spi=on
 9
10 # Enable audio (loads snd_bcm2835)
11 #dtparam=audio=on
12 dtoverlay=iqaudio-dacplus
13
14 # Additional overlays and parameters are documented
15 # /boot/firmware/overlays/README
16
17 # Automatically load overlays for detected cameras
18 camera_auto_detect=1
19
20 # Automatically load overlays for detected DSI displays
21 display_auto_detect=1
22
23 # Automatically load initramfs files, if found
24 auto_initramfs=1
25
26 # Enable DRM VC4 V3D driver
27 dtoverlay=vc4-kms-v3d,noaudio
28 max_framebuffers=2
29
30 # Don't have the firmware create an initial video= setting in cmdline.txt.
31 # Use the kernel's default instead.
32 disable_fw_kms_setup=1
33
34 # Run in 64-bit mode
35 arm_64bit=1
36
37 # Disable compensation for displays with overscan
38 disable_overscan=1
39
40 # Run as fast as firmware / board allows
41 arm_boost=1
42
43 [cm4]
44 # Enable host mode on the 2711 built-in XHCI USB controller.
45 # This line should be removed if the legacy DWC2 controller is required
46 # (e.g. for USB device mode) or if USB support is not required.
47 otg_mode=1
48
49 [all]

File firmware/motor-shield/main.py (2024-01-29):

import machine
from umqttsimple import MQTTClient
import ubinascii
import time
from motor import Motor
import json

# ### BLINK STATE ###
led = machine.Pin("LED", machine.Pin.OUT)
ledState = machine.Timer()
def blink(timer):
    led.toggle()
ledState.init(period=1000, mode=machine.Timer.PERIODIC, callback=blink)

# ### MQTT ###
SERVER = '<MQTT SERVER IP>'
CLIENT_ID = ubinascii.hexlify(machine.unique_id())
mqttClient = MQTTClient(CLIENT_ID, SERVER)
mqttClient.connect()

# ### MOTORS ###
motors = [
    Motor(0, 1),
    Motor(2, 3),
    Motor(4, 5),
    Motor(6, 7)
]
endstop = [
    machine.Pin(21, machine.Pin.IN),
    machine.Pin(20, machine.Pin.IN),
    machine.Pin(19, machine.Pin.IN),
    machine.Pin(18, machine.Pin.IN)
]
speedValTable=[0,0,0,0]
dirTable=[False, False, False, False]

def checkMotsTimer(timer):
    global speedValTable
    for i in range(4):
        motors[i].updateTimer(time.ticks_ms())
        if motors[i].timer>motors[i].duration and motors[i].targetSpeed!=0:
            print(f'motor {i} timeout')
            motors[i].Stop()
            speedValTable[i]=0
checkMotorsTimer=machine.Timer()
checkMotorsTimer.init(period=100, mode=machine.Timer.PERIODIC, callback=checkMotsTimer)

def All(direction, val):
    for i in range(4):
        motors[i].Turn(direction, val)

def StopAll():
    for i in range(4):
        motors[i].Stop()

# ### MAIN CALLBACK ###
def sub_cb(topic, msg):
    global speedValTable
    global dirTable
    # ###  PARSE JSON  ###
    data = ""
    index = ""
    for i in msg:
        data += chr(i)
    data_j = json.loads(data)
    index = int(data_j.get('index')['payload'])
    if 'stop' in data_j:
        motors[index].Stop()
        speedValTable[index]=0
    else:
        speedValTable[index]=int(data_j.get('speed')['payload'])
        dirTable[index]=data_j.get('dir')['payload']
        duration = int(data_j.get('time')['payload'])
        if motors[index].actualSpeed==0:
            motors[index].Turn(dirTable[index], speedValTable[index], time.ticks_ms())
            motors[index].setDuration(duration)
            print(f'motor {index} go at {speedValTable[index]}% during {duration}')

    # ###  PRINT TABLES  ###
    for i in range(4):
        print(dirTable[i], end=':')
        print(speedValTable[i], end=' | ')
    print('')

TOPIC = "motors"
mqttClient.set_callback(sub_cb)
mqttClient.subscribe(TOPIC)
print("Connected to %s, subscribed to %s topic" % (SERVER, TOPIC))

def main():
    while True:
        mqttClient.check_msg()

if __name__ == "__main__":
    main()

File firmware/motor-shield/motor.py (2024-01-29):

import machine

class Motor:
    """
    Driver DRV8838
    """
    def __init__(self, pwm_pin, ph_pin):
        """
        """
        self.pwm = machine.PWM(pwm_pin, freq=1000)
        self.ph = machine.Pin(ph_pin, machine.Pin.OUT)
        self.dir = 0
        self.moving = False
        self.actualSpeed = 0
        self.targetSpeed = 0
        self.isFading = False
        self.timer = 0
        self.startTimer = 0
        self.duration = 0
        self.amountFader = 77
        self.f = machine.Timer()

    def Percent(self, val):
        """
        Return the speed betwen 0 and 100 on 16bits definition
        """
        percent = (val*65536) /100
        return int(percent)

#========= TIMER =========
    # Timer are made to auto turn off the motors after n secondes
    # It corresponds to the payload in the time object inside the json sent by nodered (main.py l.73) 
    def resetTimer(self, now):
        """
        """
        print('timer reset')
        self.startTimer = now

    def updateTimer(self, now):
        """
        """
        elapse = now-self.startTimer
        self.timer=elapse

#========= MOVES =========
    def faderin(self, timer):
        """
        Fade in the speed of the motor
        smoother movements
        """
        if self.actualSpeed<self.Percent(self.targetSpeed) :
            self.actualSpeed = self.actualSpeed+self.amountFader
            self.pwm.duty_u16(self.actualSpeed)
            self.isFading = True
        else : 
            self.isFading = False
            self.f.deinit()
            print('faderIn done')
    def faderout(self, timer):
        """
        Fade out the speed of the motor
        smoother movements
        """
        if self.actualSpeed>self.Percent(self.targetSpeed) :
            self.actualSpeed = self.actualSpeed-self.amountFader
            if self.actualSpeed<0:
                self.actualSpeed = 0
            self.pwm.duty_u16(self.actualSpeed)
            self.isFading = True
        else :
            self.isFading = False
            self.moving = False
            self.f.deinit()
            print('faderOut done')

    def Turn(self, direction, speed, now):
        """
        """
        self.resetTimer(now)
        self.ph.value(direction)
        self.targetSpeed = speed

        if self.Percent(self.actualSpeed) != self.targetSpeed and not self.moving:
            self.moving = True
            self.f.init(period=5, mode=machine.Timer.PERIODIC, callback=self.faderin)

    def Stop(self):
        """
        """
        self.targetSpeed = 0
        if self.Percent(self.actualSpeed) != self.targetSpeed and self.moving:
            self.f.init(period=5, mode=machine.Timer.PERIODIC, callback=self.faderout)

    def brake(self):
        self.moving = False
        self.pwm.duty_u16(0)

#========= GETTERS =========
    def getSpeed(self):
        """
        Return actualSpeed in between 0 and 100
        """
        return self.Percent(self.actualSpeed)

    def getDir(self):
        """
        Return the actual direction
        0 → CW 
        1 → CCW
        """
        return self.ph.value()

#========= SETTERS =========    
    def setDuration(self, t):
        """
        """
        self.duration = t
        print(f'duration set to {t}')

    def setSpeed(self, sp):
        """
        """
        self.actualSpeed = sp
        self.pwm.duty_u16(self.actualSpeed)

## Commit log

2024-01-29 first push
    [bottom.dxf, config.txt, endstop_nut_.stl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]
2024-04-05 Update main.py
    change snapshots timing for sensors
